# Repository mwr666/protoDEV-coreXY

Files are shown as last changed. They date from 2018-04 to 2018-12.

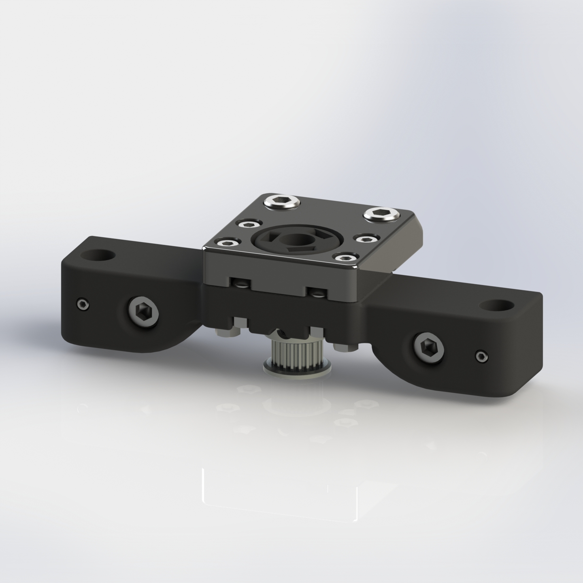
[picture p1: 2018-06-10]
render/z_axis_bottom_assembly_00.JPG

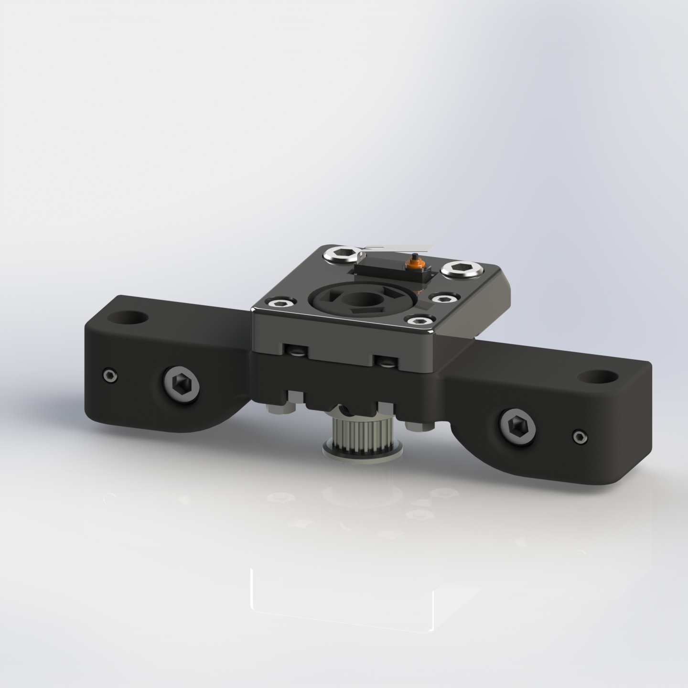
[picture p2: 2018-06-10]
render/z_axis_bottom_endstop_assembly_00.JPG

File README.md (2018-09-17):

# protoDEV coreXY
<b>coreXY direct drive extruder 3D printer running Smootieware firmware</b>

-------------------------------------------------------------------------------------------- 

<b>About:</b>
 
 What is working here? 

Hmmm... most important... it can 3d-print 24/7. 

This is not an another incomplete "work in progress" project. It's a work in progress project that has improvement in mind. 

I'm into 3d printing for few years, and active building 3d printers for most of that time. Learned a lot thanks to the community... 
and specially from community based systems like Prusa's. Internet is a place were some got news, youtube, porn... 
and some having nerd stuff... software, mechanical, electrical and electronics articles, blogs, vlogs, faqs etc. 
If you are a tech Nerd just like me, you can find tons of very interesting educational articles that can build up your knowledge until... 
for me everything ended up here on GitHub. Why? because was living the 3d printer hype and tested all the bullshit and non-bulshit projects on te planet. 

Now it's time to share some of the knowledge just like all those people all over the world shared with me. 
 
 My goal is to gather some people that will/want to build, use and improve the project.
 I've spent over 3 months working on the Cad3D part (SolidWorks) of the project to make parts simple to print and simple for makers to assembly.
 The most of those 3 months was a the path of math, symetry, mechanics... and off course... aggressive wife :P
 Then had to spent some time working on some moddifications to Smoothieware firmware and hardware just to suit the system.
 After that been studying how printer moves in slo-mo to further improve the config and mechanics.
 After builiding & testing several machine variations, got to a place where the machine just after proper setup and calibration works without ANY failure within last several months.
 
 My main goal for the system was to print with speed and quality parameters equal or beyond the market systems at under 1000 euro price tag. 
 
-------------------------------------------------------------------------------------------- 
 
<b>Features:</b>

 * build plate 245 x 245 x 300 mm ( X x Y x Z ) 
 * 32bit Smoothieware firmware for smooth motion
 * e3d volcano hotend with hartened steel 0.4mm nozzle
 * TMC2208 silent stepper drivers - spread cycle setup with step interpolarisation 1/256 
 * geared (3:1) direct drive extuder with Bondtech dual drive gears(simpler and more reliable printing then bowden)
 * max speed up to 300mm/s 
 * heated build plate with PET film surface for superb material adhesion 
 * support of multiple filament types (PLA, PET, TPU)
 * filament run-out sensor
 * coreXY with proper belt alignment for hi-torque and stiffness
 * hi-flow quality hotend (e3d hotend with volcano heat block) for high quality and fast printing
 * all axis with 2x higher mechanical resolution at same step rate (0.9deg 1/8 step = 1.8deg 1/16 step)
 * one motor doubble z-axis (no shaft sync problems)
 * all axis motors mounted at bottom of printer to lower the center of gravity  
 * all of non-printed parts was selected to be worldwide availabe and have resonable price to quality ratio.
 * enclosure
 * automatic nozzle cleaner
 * automatic parts removal ( if got time or need for this add on to work - i've designed it and printed just waiting for software )

-------------------------------------------------------------------------------------------- 
 
<b>TODO:</b>

 * add enclosure files prepared for laser cutting

 * find quiet print cooling fans replacement
 
 * enclosure over-temperature control
 
 * 3rd party controler boards support (actual controler price to high?)
 
 * apr addon (automatic parts removal) test and firmware development for batch 3d printing
 
 * <font color="green"><s>add latest 24V-hiwin-tmc2208 project files</s> <b>*done</b></font> 
 
 * cleanup in filenames / solidworks project
 
 * <font color="green"><s>cleanup in stl folder (right now it's pure project .stl dump, so lots of files not need to be printed)</s> <b>*done</b></font>
 
 * heatbed build instructions
 
 * <font color="green"><s>list of parts</s> <b>*done</b></font>
 
 * build instruction
 
 * firmware/software manual
 
 * BOM for all non-printed parts
 
*  <font color="green"><s>test 24V system theoretical print speed >375mm/s</s> <b>*done & working</b></font>
 
 * <font color="green"><s>build a test Hiwin x-axis</s> <b>*done & working</b></font>
 
*  <font color="red"><s>build a test carbon fiber rods + igus bearings x-axis</s> <b>*done - don't like it</b></font>
 
 * ???

--------------------------------------------------------------------------------------------
 
<b>Contact: mw@protodev.pl</b>

<b>https://www.thingiverse.com/thing:2119644 big thx for superb spool system from Spanner Hands http://www.spannerhands.co.uk/<b>

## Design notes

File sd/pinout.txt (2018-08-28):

P1.21		LED3		Pad4		led4		            h/w PWM capable. can be free if leds_disable is set true in config.
P1.24		-		    Pad7		alpha_min_endstop		h/w PWM capable
P3.26		-			Pad14		spare					used for encoder pin for all panels, h/w PWM capable

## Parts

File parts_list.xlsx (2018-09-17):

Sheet: part list
no. | part name | type | subtype | attribute | qty. | pcs/pack | price per pack(PLN) | qty. | total (PLN) | shop link
1 | alu square pipe | shop part | 20x20mm | 373mm | 1 |  |  |  | 0
2 | alu-profil | openbeam | 1515 | 240mm | 1 |  |  |  | 0
3 | alu-profil | T-Slot | 2020 | 360mm | 15 |  |  |  | 0
4 | alu-profil | T-Slot | 2020 | 600mm | 4 |  |  |  | 0
5 | alu-profil | T-Slot | 2020 | 95mm | 1 |  |  |  | 0
6 | corner | T-Slot | 2020 |  | 34 |  |  |  | 0
7 | 3-way connector | T-Slot | 2020 |  | 8 |  |  |  | 0
8 | half-nut | T-Slot | M3 |  | 52 |  |  |  | 0
9 | nut | T-Slot | M3 |  | 10 |  |  |  | 0
10 | nut | T-Slot | M5 |  | 108 |  |  |  | 0
11 | lead screw | shop part | TR8x8 | 400mm | 2 | 1 | 40 | 2 | 80 | https://blackfrog.pl/sruba-trapezowa-t8-z-nakretka-fi-8mm-skok-1mm-dl-400-mm-p-710.html
12 | leveling nut | shop part | M3 |  | 3 |  |  |  | 0
13 | bed spring | shop part |  |  | 3 |  |  |  | 0
14 | anti-backlash nut | shop part | TR8x8 |  | 2 | 1 | 25 | 2 | 50 | https://blackfrog.pl/nakretka-bezluzowa-sruba-t8-skok-8-mm-p-1149.html
15 | laminator roller | shop part |  |  | 2 |  |  |  | 0
16 | glass | shop part | borosilicate | 280x280mm | 1 | 1 | 195 | 1 | 195 | local glass shop
17 | thermal cover | shop part | cork | 280x280mm | 1 |  |  |  | 0
18 | heater | shop part | silicone | 280x280mm | 1 |  |  |  | 0
19 | e3d volcano block | shop part |  |  | 1 | 1 | 95 | 1 | 95 | https://blackfrog.pl/blok-grzejny-e3d-volcano-p-988.html
20 | e3d v6 direct full kit | shop part |  |  |  | 1 | 280 | 1 | 280 | https://blackfrog.pl/glowica-e3d-v6-175-12v-direct-full-kit-p-245.html
21 | volcano 0.4mm hartened steel nozzle | shop part |  |  |  | 1 | 95 | 1 | 95 | https://blackfrog.pl/dysza-volcano-e3d-stal-utwardzana-175-04-p-982.html
22 | e3d heater cartige 104GT-2 | shop part |  |  |  | 1 | 31 | 1 | 31 | https://blackfrog.pl/termistor-semitec-104gt-2-w-obudowie-p-783.html
23 | heater cartige | shop part | 12V | 40W | 1 |  |  |  | 0
24 | thermistor | shop part | Semitec |  | 2 |  |  |  | 0
25 | e3d Semitec thermistor cartige | shop part |  |  | 1 |  |  |  | 0
26 | door_hinge_shaft (alu-rod) | shop part | 5mm | 37mm | 2 |  |  |  | 0
27 | alu rod | shop part | 5mm | 32mm | 1 |  |  |  | 0
28 | alu rod | shop part | 5mm | 490mm | 2 |  |  |  | 0
29 | steel rod | shop part | 3mm | 30mm | 2 |  |  |  | 0
30 | steel rod | shop part | 8mm | 390mm | 4 |  |  |  | 0
31 | steel rod | shop part | 8mm | 217mm | 2 |  |  |  | 0
32 | fitting | shop part | PTFE | PC6-M6 | 2 |  |  |  | 0
33 | microswitch endstop | shop part |  |  | 4 |  |  |  | 0
34 | microswitch endstop with roller | shop part |  |  | 1 |  |  |  | 0
35 | NEMA17 200 step stepper motor | shop part | 17HS1070-C5X | 34mm | 1 |  |  |  | 0
36 | NEMA17 400 step stepper motor | shop part | 42BYGHM809 | 48mm | 3 |  |  |  | 0
37 | heatsink | shop part |  | 40x40x11mm | 3 |  |  |  | 0
38 | geared motor | shop part | XH-25D | 6VDC 275RPM | 1 |  |  |  | 0
39 | extruder gear | shop part | MK7 |  | 1 | 1 | 7.99 | 1 | 7.99 | http://electropark.pl/radelka/4433-kolo-zebate-ekstrudera-mk7-radelko.html
40 | fan | shop part | 3010 | 12V | 3 |  |  |  | 0
41 | extruder spring | shop part |  |  | 2 |  |  |  | 0
42 | diode smoother board | shop part | MKS |  | 4 | 1 | 16 | 4 | 64 | https://blackfrog.pl/mks-smoother-filtr-diodowy-p-1057.html
43 | lcd control panel | shop part | Sumbeam 2.0 |  | 1 |  |  |  | 0
44 | 3rd party smoothieboard rev.C | shop part | Sumbeam 2.0 |  | 1 |  |  |  | 0
45 | neo_magnet_4mm_x_4mm | shop part |  |  | 6 |  |  |  | 0
46 | dial_sticker_feet | shop part |  |  | 4 |  |  |  | 0
47 | tower pro sg90 hobby servo (full kit) | shop part |  |  | 1 |  |  |  | 0
48 | nozzle cleaner rubber | shop part |  |  | 1 |  |  |  | 0
49 | expansion board | private part | Sumbeam 2.0 |  | 1 |  |  |  | 0
50 | memory card | shop part | microSD | <4GB | 1 |  |  |  | 0
51 | memory card | shop part | SDcard | <32GB | 1 |  |  |  | 0
52 | stepper driver with heatsink | shop part | TMC2208 |  | 4 | 1 | 46 | 4 | 184 | https://blackfrog.pl/silentstepstick-tmc2208-watterott-p-1271.html
53 | power socket | shop part | 3 Pin IEC320 C14 | 10A 250V | 1 |  |  |  | 0
54 | psu | shop part | Meanwell | 12V 300W | 1 | 1 | 120 | 1 | 120 | http://allegro.pl/zasilacz-led-modulowy-montazowy-12v-300w-25a-i7308720266.html
55 | psu | shop part | Bergmen | 24V 150W | 1 | 1 | 240.9 | 1 | 240.9 | https://sklep.bergmen.pl/storm-150w-24vdc-6-25a-ip68,3,2472,1605
56 | linear bearing | bearing | LM8UU |  | 4 | 1 | 2.75 | 4 | 11 | http://allegro.pl/lozyska-liniowe-fi8-8mm-lm8uu-reprap-drukarka-3d-i6099245510.html
57 | ball bearing | bearing | 608ZZ |  | 4 | 1 | 1 | 4 | 4 | http://allegro.pl/608-zz-lozysko-kulkowe-8x22x7-mm-cnc-fv-23-i6754089162.html
58 | ball bearing | bearing | F623ZZ |  | 4 | 1 | 2.8 | 4 | 11.2 | http://allegro.pl/f623-zz-lozysko-z-kolnierzem-flansza-3x10x4-reprap-i6487218476.html
59 | ball bearing | bearing | 625zz |  | 10 | 1 | 1 | 10 | 10 | http://allegro.pl/625-zz-lozysko-kulkowe-5x16x5-mm-cnc-fv-23-i6487158324.html
60 | ball bearing | bearing | 623zz |  | 17 | 1 | 1 | 17 | 17 | http://allegro.pl/623-zz-lozysko-kulkowe-3x10x4-mm-cnc-fv-23-i6487155806.html
61 | build plate belt | belt | PET | 242mm | 1 |  |  |  | 0
62 | belt | GT2 | closed-loop | 120-130mm | 2 | 1 | 10 | 2 | 20 | http://allegro.pl/pasek-zebaty-petla-130-mm-gt2-szer-6mm-reprap-cnc-i7169467426.html
63 | belt | GT2 | closed-loop | 720mm | 1 | 1 | 22 | 1 | 22 | http://allegro.pl/pasek-zebaty-petla-752-mm-gt2-szer-6mm-reprap-cnc-i7169534315.html
64 | belt | GT2 | open-loop | <1422 | 2 | 1000 | 6.9 | 2 | 13.8 | http://allegro.pl/pasek-zebaty-gt2-6mm-100cm-reprap-drukarka-3d-i7270779540.html
65 | pully | GT2 | 20T | 8mm | 2 | 1 | 13 | 2 | 26 | https://blackfrog.pl/zebatka-gt2-20-zebow-otwor-fi-8-pasek-6-mm-p-158.html
66 | pully | GT2 | 20T | 5mm | 7 | 1 | 8.49 | 7 | 59.43 | http://allegro.pl/zebatka-reprap-gt2-20-zebow-5mm-3d-cnc-i6099125153.html
67 | rail | MGH | 12H | 360mm | 3 | 100 | 70 | 4 | 280 | https://blackfrog.pl/szyna-liniowa-mgnr-12-dlugosc-10-cm-p-768.html
68 | carriage | MGH | 12H |  | 3 | 1 | 165 | 2 | 330 | https://blackfrog.pl/wozek-hiwin-mgn12h-p-765.html
69 | hex nut | nut | M3 |  | 74 | 10 | 1.5 | 8 | 12 | http://allegro.pl/nakretki-nakretka-m3-czarna-10szt-komplet-oksyda-i5080287746.html
70 | prevailing torque hex nut | nut | M8 |  | 1 | 10 | 4.8 | 1 | 4.8 | http://allegro.pl/nakretka-samohamowna-czarna-oksyda-m8-10szt-i6842846781.html
71 | socket head cap screw | screw | M8 | 80mm | 1 | 5 | 5 | 1 | 5 | http://allegro.pl/sruba-imbusowa-czarna-m8x80-gniazdo-imbus-5szt-i6596358554.html
72 | socket head cap screw | screw | M5 | 25mm | 4 | 10 | 3.2 | 1 | 3.2 | http://allegro.pl/sruba-imbusowa-czarna-m5x25-gniazdo-imbus-10szt-i5045808605.html
73 | socket head cap screw | screw | M5 | 20mm | 16 | 10 | 2.9 | 2 | 5.8 | http://allegro.pl/sruba-imbusowa-czarna-m5x20-gniazdo-imbus-10szt-i7140410516.html
74 | hex cap screw | screw | M5 | 16mm | 1 | 1 | 1 | 1 | 1
75 | socket head cap screw | screw | M5 | 10mm | 5 | 10 | 2.5 | 1 | 2.5 | http://allegro.pl/sruba-imbusowa-czarna-m5x10-gniazdo-imbus-10szt-i5044828525.html
76 | socket head cap screw | screw | M5 | 8mm | 76 | 10 | 2.6 | 8 | 20.8 | http://allegro.pl/sruba-imbusowa-czarna-m5x8-gniazdo-imbus-10szt-i5045808558.html
77 | socket head cap screw | screw | M5 | 6mm | 14 | 10 | 2.8 | 2 | 5.6 | http://allegro.pl/sruba-imbusowa-czarna-m5x6-gniazdo-imbus-10szt-i5045808600.html
78 | socket set screw flat point | screw | M4 | 6mm | 32 |  |  |  | 0
79 | socket head cap screw | screw | M3 | 45mm | 23 | 5 | 2.9 | 5 | 14.5 | http://allegro.pl/sruba-imbusowa-czarna-m3x45-gniazdo-imbus-5szt-i5039141859.html
80 | socket head cap screw | screw | M3 | 40mm | 12 | 5 | 2.4 | 3 | 7.2 | http://allegro.pl/sruba-imbusowa-czarna-m3x40-gniazdo-imbus-5szt-i5063374831.html
81 | socket head cap screw | screw | M3 | 35mm | 14 | 10 | 3.3 | 2 | 6.6 | http://allegro.pl/sruba-imbusowa-czarna-m3x35-gniazdo-imbus-10szt-i5176356584.html
82 | socket head cap screw | screw | M3 | 25mm | 12 | 10 | 2.8 | 2 | 5.6 | http://allegro.pl/sruba-imbusowa-czarna-m3x25-gniazdo-imbus-10szt-i5415086316.html
83 | socket button head cap screw | screw | M3 | 25mm | 8 | 10 | 1.6 | 1 | 1.6 | http://allegro.pl/sruba-kulista-czarna-m3x25-gniazdo-imbus-10szt-i5214620250.html
84 | socket button head cap screw | screw | M3 | 20mm | 22 | 10 | 1.5 | 3 | 4.5 | http://allegro.pl/sruba-kulista-czarna-m3x20-gniazdo-imbus-10szt-i5214620056.html
85 | socket head cap screw | screw | M3 | 20mm | 37 | 10 | 2.5 | 4 | 10 | http://allegro.pl/sruba-imbusowa-czarna-m3x20-gniazdo-imbus-10szt-i5057841873.html
86 | socket head cap screw | screw | M3 | 16mm | 10 | 10 | 2.2 | 1 | 2.2 | http://allegro.pl/sruba-imbusowa-czarna-m3x16-gniazdo-imbus-10szt-i5184033908.html
87 | socket button head cap screw | screw | M3 | 16mm | 16 | 10 | 1.3 | 2 | 2.6 | http://allegro.pl/sruba-kulista-czarna-m3x16-gniazdo-imbus-10szt-i5214620038.html
88 | socket button head cap screw | screw | M3 | 12mm | 6 | 10 | 1.1 | 1 | 1.1 | http://allegro.pl/sruba-kulista-czarna-m3x12-gniazdo-imbus-10szt-i5142905904.html
89 | socket head cap screw | screw | M3 | 10mm | 10 | 10 | 1.7 | 1 | 1.7 | http://allegro.pl/sruba-imbusowa-czarna-m3x10-gniazdo-imbus-10szt-i5006971342.html
90 | socket button head cap screw | screw | M3 | 10mm | 34 | 10 | 1.1 | 4 | 4.4 | http://allegro.pl/sruba-kulista-czarna-m3x10-gniazdo-imbus-10szt-i5089594834.html
91 | socket button head cap screw | screw | M3 | 8mm | 29 | 10 | 1.5 | 3 | 4.5 | http://allegro.pl/sruba-kulista-czarna-m3x8-gniazdo-imbus-10szt-i5315915867.html
92 | socket head cap screw | screw | M3 | 8mm | 69 | 10 | 1.9 | 7 | 13.3 | http://allegro.pl/sruba-imbusowa-czarna-m3x8-gniazdo-imbus-10szt-i5113065217.html
93 | socket set screw flat point | screw | M3 | 6mm | 39 | 10 | 1.4 | 4 | 5.6 | http://allegro.pl/sruba-dociskowa-czarna-m3x6-gniazdo-imbus-10szt-i5088078246.html
94 | socket head cap screw | screw | M3 | 6mm | 6 | 10 | 1.9 | 1 | 1.9 | http://allegro.pl/sruba-imbusowa-czarna-m3x6-gniazdo-imbus-10szt-i5717390190.html
95 | socket button head cap screw | screw | M3 | 6mm | 27 | 10 | 1 | 3 | 3 | http://allegro.pl/sruba-kulista-czarna-m3x6-gniazdo-imbus-10szt-i6789930676.html
96 | socket head cap screw | screw | M2.5 | 12mm | 5 | 10 | 2.3 | 1 | 2.3 | http://allegro.pl/sruba-imbusowa-czarna-m2-5x12-gniazdo-imbus-10szt-i5214620364.html
97 | flat washer | washer | M3 |  | 8 | 20 | 1.2 | 1 | 1.2 | http://allegro.pl/podkladka-czarna-m3-komplet-20szt-oksyda-i5080289361.html
98 | spring washer (from NEMA 17 stepper motor) | shop part |  |  | 1 |  |  |  | 0
99 | bed_clamp_bottom.STL | printed part |  |  | 3 |  |  |  | 0
100 | bed_clamp_top.STL | printed part |  |  | 3 |  |  |  | 0
101 | top_base.STL | printed part |  |  | 2 |  |  |  | 0
102 | lift_right_side_base.STL | printed part |  |  | 1 |  |  |  | 0
103 | z_axis_endstop_bumper.STL | printed part |  |  | 1 |  |  |  | 0
104 | bed_clamp_mount_side.STL | printed part |  |  | 1 |  |  |  | 0
105 | bed_clamp_mount_side_cover.STL | printed part |  |  | 1 |  |  |  | 0
106 | bed_clamp_mount_side2_cover.STL | printed part |  |  | 1 |  |  |  | 0
107 | bed_clamp_mount_side2.STL | printed part |  |  | 1 |  |  |  | 0
108 | lift_left_side_base.STL | printed part |  |  | 1 |  |  |  | 0
109 | back_left_roller_motor_mount.STL | printed part |  |  | 1 |  |  |  | 0
110 | back_right_roller_mount.STL | printed part |  |  | 1 |  |  |  | 0
111 | front_right_roller_mount.STL | printed part |  |  | 1 |  |  |  | 0
112 | front_left_roller_mount.STL | printed part |  |  | 1 |  |  |  | 0
113 | apr_shaft_beam.STL | printed part |  |  | 2 |  |  |  | 0
114 | apr_gears.STL | printed part |  |  | 1 |  |  |  | 0
115 | bottom_base.STL | printed part |  |  | 1 |  |  |  | 0
116 | blocker_cover.STL | printed part |  |  | 1 |  |  |  | 0
117 | blocker_lead_screw_8mm.STL | printed part |  |  | 1 |  |  |  | 0
118 | bottom_base_endstop.STL | printed part |  |  | 1 |  |  |  | 0
119 | blocker_cover_endstop.STL | printed part |  |  | 1 |  |  |  | 0
120 | blocker_lead_screw_8mm.STL | printed part |  |  | 1 |  |  |  | 0
121 | motor_holder_cover.STL | printed part |  |  | 2 |  |  |  | 0
122 | motor_holder.STL | printed part |  |  | 2 |  |  |  | 0
123 | z_motor_holder_top_v2.STL | printed part |  |  | 1 |  |  |  | 0
124 | z_motor_holder_v2.STL | printed part |  |  | 1 |  |  |  | 0
125 | z_motor_holder_cover_v2.STL | printed part |  |  | 1 |  |  |  | 0
126 | z_motor_holder_top_cover_v2.STL | printed part |  |  | 1 |  |  |  | 0
127 | z_axis_square_pipe_mount.STL | printed part |  |  | 2 |  |  |  | 0
128 | motor_block_bearing.STL | printed part |  |  | 4 |  |  |  | 0
129 | motor_block_bearing_cover.STL | printed part |  |  | 2 |  |  |  | 0
130 | printable_20T_GT2_idler_tooth.STL | printed part |  |  | 6 |  |  |  | 0
131 | printable_20T_GT2_idler_smooth.STL | printed part |  |  | 2 |  |  |  | 0
132 | idler_holder_doubble_left_v3.STL | printed part |  |  | 1 |  |  |  | 0
133 | idler_holder_doubble_right_v3.STL | printed part |  |  | 1 |  |  |  | 0
134 | rail_holder_left_front.STL | printed part |  |  | 1 |  |  |  | 0
135 | rail_holder_left_back.STL | printed part |  |  | 1 |  |  |  | 0
136 | rail_holder_endstop.STL | printed part |  |  | 1 |  |  |  | 0
137 | rail_holder_right_back.STL | printed part |  |  | 1 |  |  |  | 0
138 | y_carrige_cover_left.STL | printed part |  |  | 1 |  |  |  | 0
139 | y_carrige_cover_right.STL | printed part |  |  | 1 |  |  |  | 0
140 | y_carriage_left.STL | printed part |  |  | 1 |  |  |  | 0
141 | y_carriage_right.STL | printed part |  |  | 1 |  |  |  | 0
142 | hiwin_block.STL | printed part |  |  | 1 |  |  |  | 0
143 | carriage_cable_holder.STL | printed part |  |  | 1 |  |  |  | 0
144 | 33tooth_spur_gear.STL | printed part |  |  | 1 |  |  |  | 0
145 | fan_mount_v12.STL | printed part |  |  | 1 |  |  |  | 0
146 | fan_cover_front.STL | printed part |  |  | 1 |  |  |  | 0
147 | fan_cover.STL | printed part |  |  | 1 |  |  |  | 0
148 | button.STL | printed part |  |  | 1 |  |  |  | 0
149 | gear_cover.STL | printed part |  |  | 1 |  |  |  | 0
150 | geared_extruder_3to1_hiwin.STL | printed part |  |  | 1 |  |  |  | 0
151 | ac_plug_mount_cover.STL | printed part |  |  | 1 |  |  |  | 0
152 | ac_plug_mount_base.STL | printed part |  |  | 1 |  |  |  | 0
153 | mks_4x_smoother_mount.STL | printed part |  |  | 1 |  |  |  | 0
154 | mks_4x_smoother_mount_spacer.STL | printed part |  |  | 1 |  |  |  | 0
155 | board_holder.STL | printed part |  |  | 1 |  |  |  | 0
156 | vent_board_back_v2.STL | printed part |  |  | 1 |  |  |  | 0
157 | filament_sensor_holder.STL | printed part |  |  | 1 |  |  |  | 0
158 | filament_sensor_base_spool_holder.STL | printed part |  |  | 1 |  |  |  | 0
159 | filament sensor_cover_spool_holder.STL | printed part |  |  | 1 |  |  |  | 0
160 | lid_v3_0_1kg_Spool.STL | printed part |  |  | 1 |  |  |  | 0
161 | base_v3_0_1kg_Spool.STL | printed part |  |  | 1 |  |  |  | 0
162 | 20x20_T_Slot_MOUNT_v1_0.STL | printed part |  |  | 1 |  |  |  | 0
163 | clasp_bracket_v2_0.STL | printed part |  |  | 1 |  |  |  | 0
164 | semi_flex_clasp_v2_0.STL | printed part |  |  | 1 |  |  |  | 0
165 | flex_seal_v3_0_1kg_Spool.STL | printed part |  |  | 1 |  |  |  | 0
166 | panel_cover_front.STL | printed part |  |  | 1 |  |  |  | 0
167 | panel_cover_bottom.STL | printed part |  |  | 1 |  |  |  | 0
168 | arrow_button.STL | printed part |  |  | 2 |  |  |  | 0
169 | blank_button.STL | printed part |  |  | 2 |  |  |  | 0
170 | reset_button.STL | printed part |  |  | 1 |  |  |  | 0
171 | psu_holder.STL | printed part |  |  | 1 |  |  |  | 0
172 | extruder_cable_cover.STL | printed part |  |  | 1 |  |  |  | 0
173 | magnetic_bottom.STL | printed part |  |  | 1 |  |  |  | 0
174 | magnetic_top.STL | printed part |  |  | 1 |  |  |  | 0
175 | handle_front.STL | printed part |  |  | 1 |  |  |  | 0
176 | door_hinge_1b.STL | printed part |  |  | 2 |  |  |  | 0
177 | 2020_140mm_fan_mount.STL | printed part |  |  | 1 |  |  |  | 0
178 | 2020_140mm_fan_mount_mirror.STL | printed part |  |  | 1 |  |  |  | 0
179 | 2020_top_cover_corner.STL | printed part |  |  | 4 |  |  |  | 0
180 | 2020_cover_middle_section.STL | printed part |  |  | 2 |  |  |  | 0
181 | 2020_cover_middle_Handle_section.STL | printed part |  |  | 2 |  |  |  | 0
182 | 2020_bottom_corner_cover.STL | printed part |  |  | 4 |  |  |  | 0
183 | 2020_cover_middle_section.STL | printed part |  |  | 4 |  |  |  | 0
184 | 2020_corner_cover_mount_top_spool_holder.STL | printed part |  |  | 1 |  |  |  | 0
185 | 2020_corner_cover_mount.STL | printed part |  |  | 4 |  |  |  | 0
186 | 2020_corner_cover_mount_top.STL | printed part |  |  | 4 |  |  |  | 0
187 | 2020_corner_cover_mount_top_screw_hole.STL | printed part |  |  | 3 |  |  |  | 0
188 | handle.STL | printed part |  |  | 2 |  |  |  | 0
189 | door_hinge_1a.STL | printed part |  |  | 2 |  |  |  | 0
190 | wiper_v2.STL | printed part |  |  | 1 |  |  |  | 0
191 | 2020_servo_holder.STL | printed part |  |  | 1 |  |  |  | 0
192 | cover_side_plate | laser-cut |  |  | 1 |  |  |  | 0
193 | cover_ac_power_in_side_plate | laser-cut |  |  | 1 |  |  |  | 0
194 | cover_back_plate | laser-cut |  |  | 1 |  |  |  | 0
195 | cover_front_plate | laser-cut |  |  | 1 |  |  |  | 0
196 | cover_middle_plate | laser-cut |  |  | 1 |  |  |  | 0
197 | door_plate | laser-cut |  |  | 1 |  |  |  | 0
198 | cover_top_plate | laser-cut |  |  | 1 |  |  |  | 0
199 | cover_bottom_plate | laser-cut |  |  | 1 |  |  |  | 0
 |  |  |  |  |  |  |  |  | 2401.82
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

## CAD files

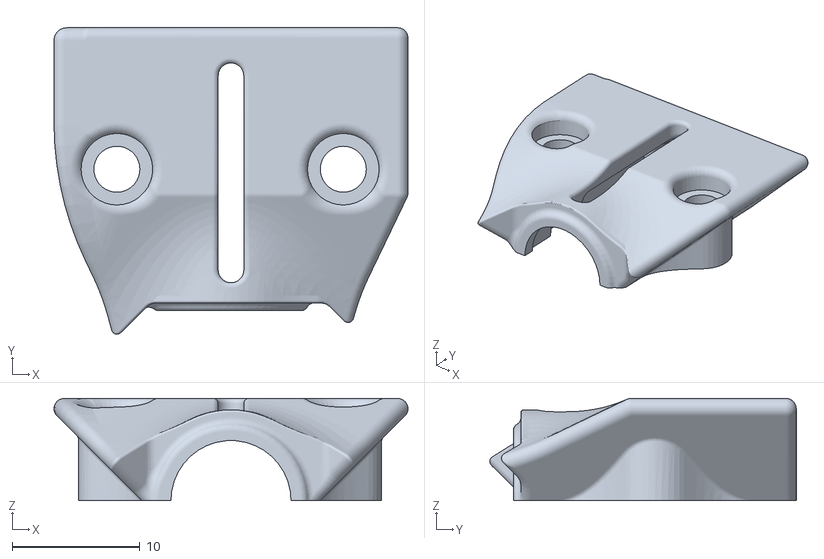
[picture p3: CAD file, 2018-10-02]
stl/x_axis_carriage_plate/parts/bondtech_gears_extruder/bondtech_main_block_cover_v3.STL
27.7 x 24.0 x 7.99

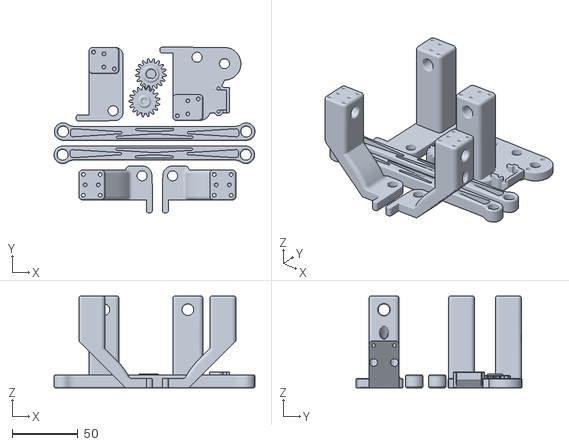
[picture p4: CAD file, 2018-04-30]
stl/apr_parts_plate/apr_parts_plate.stl
153.4 x 126.7 x 70.0

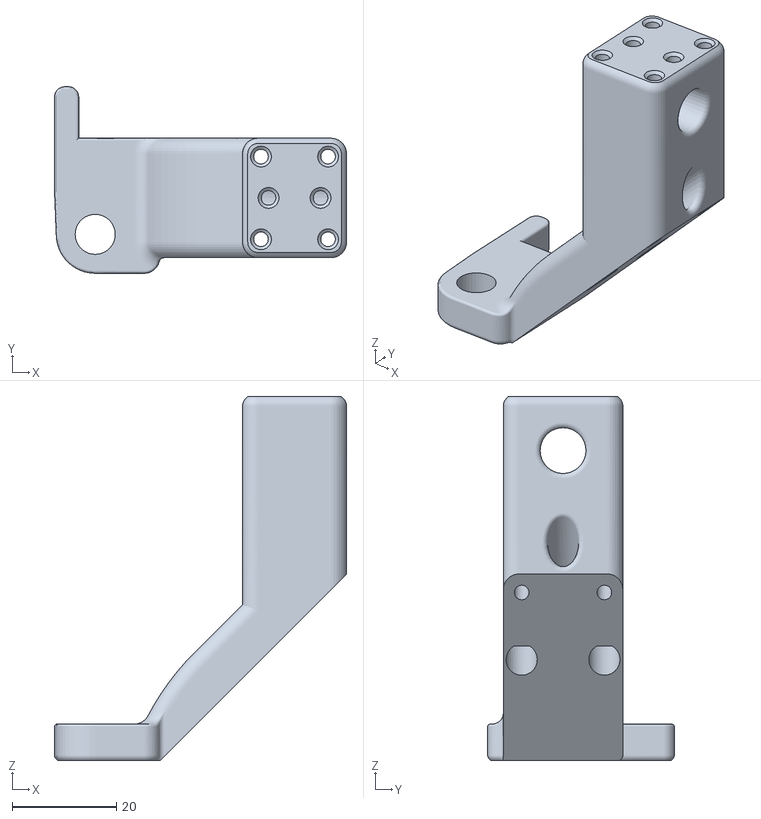
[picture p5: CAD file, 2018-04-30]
stl/apr_parts_plate/parts/back_right_roller_mount.STL
56.2 x 35.9 x 70.0

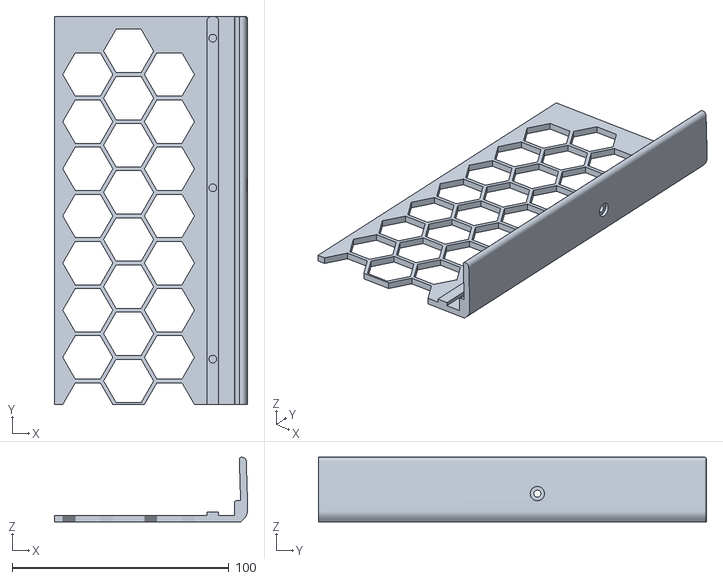
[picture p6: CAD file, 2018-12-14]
stl/inner_back_top_left.STL
89.0 x 178.9 x 29.8

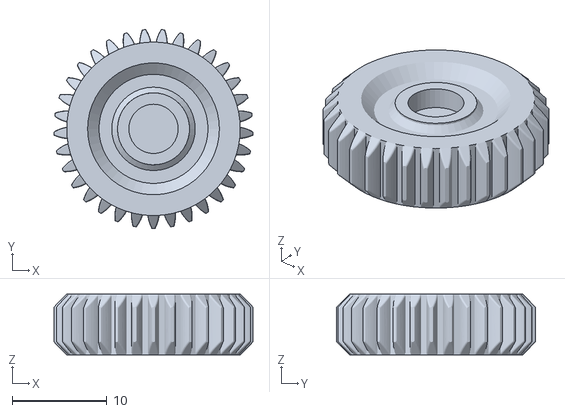
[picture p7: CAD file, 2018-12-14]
stl/x_axis_carriage_plate/parts/bondtech_gears_extruder/bondtech_gear_v2.STL
21.0 x 21.0 x 6.40

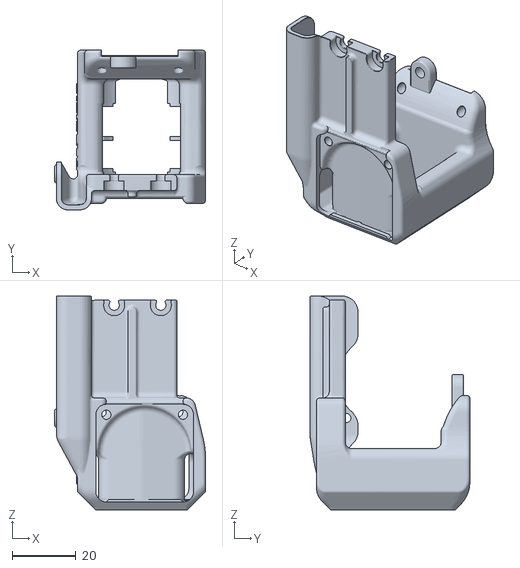
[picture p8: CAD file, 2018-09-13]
stl/x_axis_carriage_plate/parts/fan_mount_v12.STL
47.3 x 50.0 x 67.0

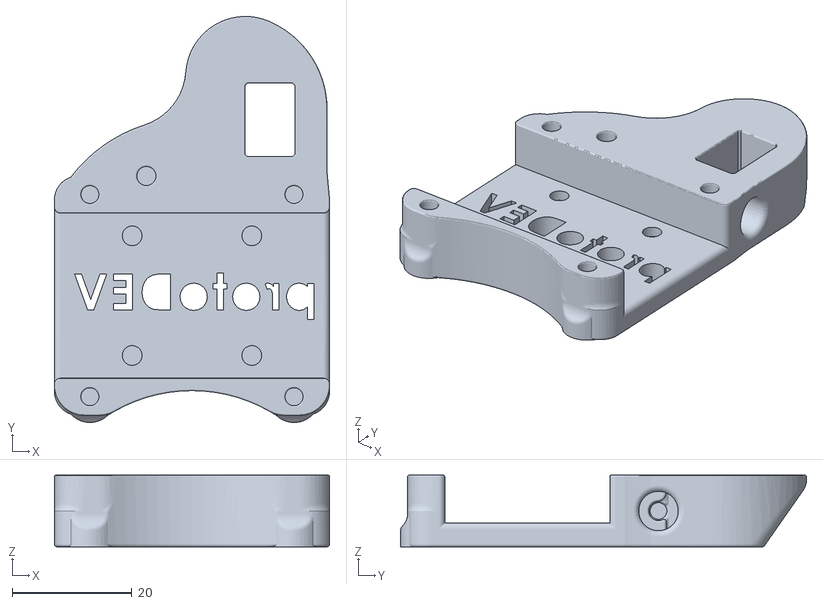
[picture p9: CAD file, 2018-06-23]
stl/y_axis_parts_plate/parts/y_carriage_cover_right.STL
46.0 x 67.9 x 12.0

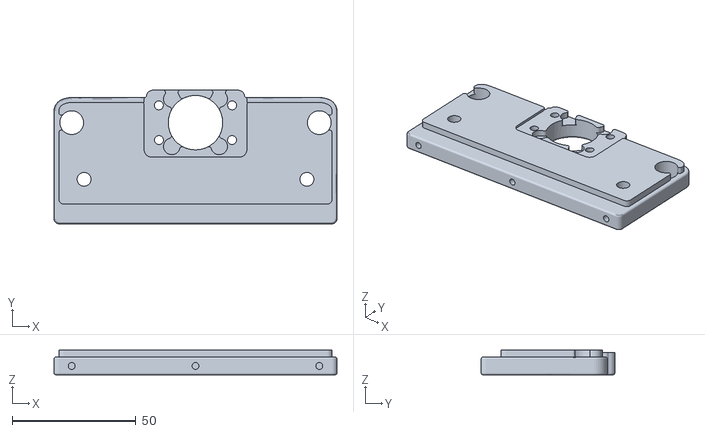
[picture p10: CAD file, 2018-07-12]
stl/z_axis_parts_plate/parts/blocker_cover.STL
114.3 x 54.0 x 10.0

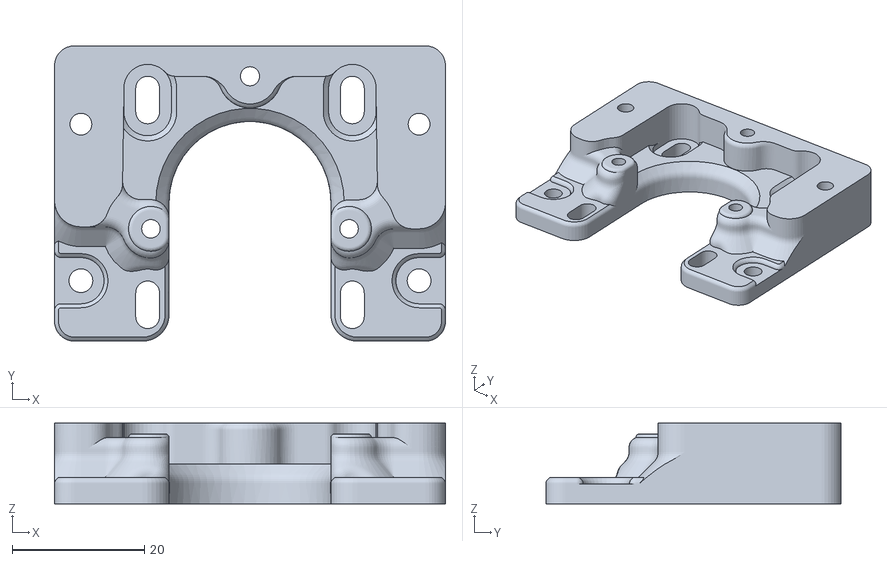
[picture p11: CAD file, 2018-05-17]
stl/z_axis_tensioner_parts_plate/parts/z_motor_holder_cover_v2.STL
59.2 x 44.7 x 12.2

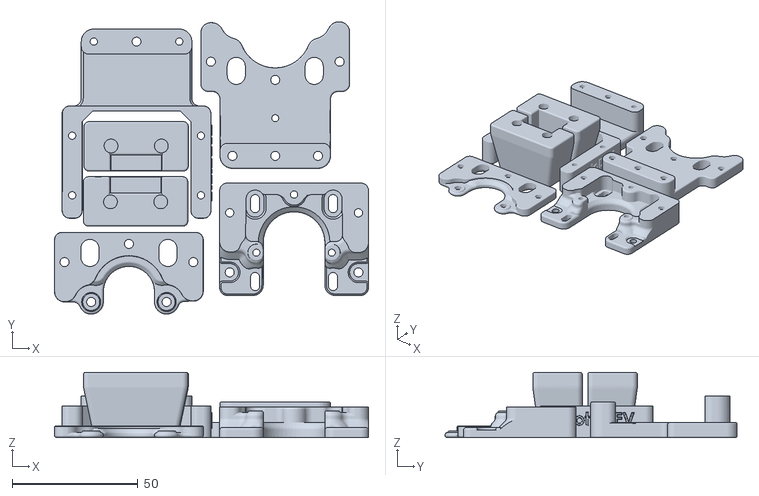
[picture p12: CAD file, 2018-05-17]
stl/z_axis_tensioner_parts_plate/z_axis_tensioner_parts_plate.stl
124.9 x 116.3 x 26.0

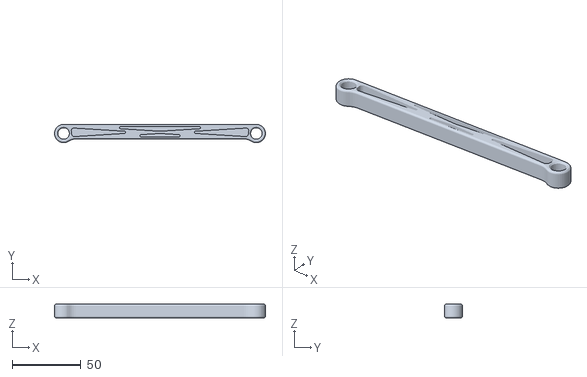
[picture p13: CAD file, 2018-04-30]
stl/apr_parts_plate/parts/apr_shaft_beam.STL
153.1 x 13.3 x 10.0

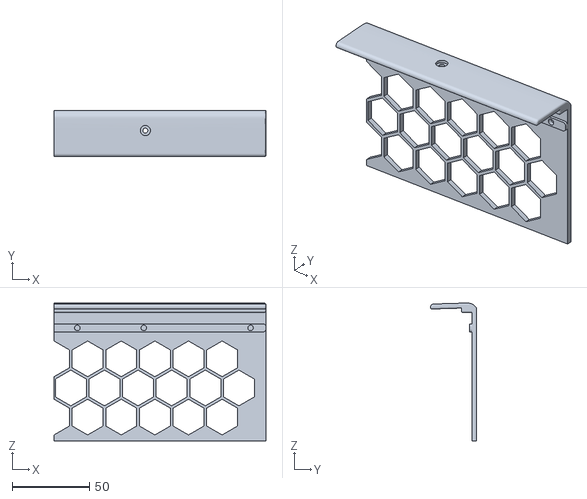
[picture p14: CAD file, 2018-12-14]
stl/inner_back_top_right.STL
137.1 x 29.8 x 89.0

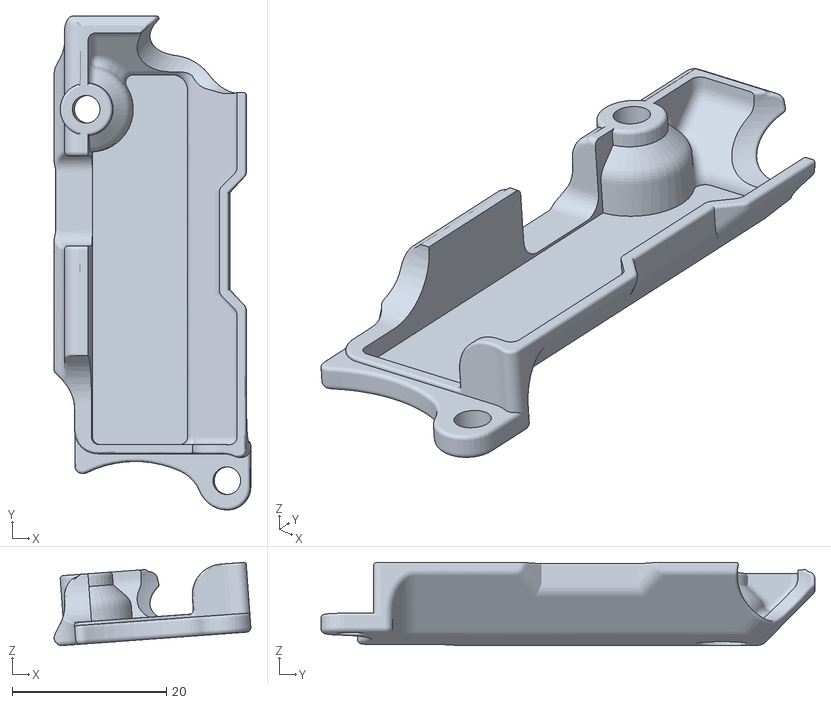
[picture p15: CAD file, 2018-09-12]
stl/x_axis_carriage_plate/parts/extruder_cable_cover.STL
25.5 x 64.1 x 10.8

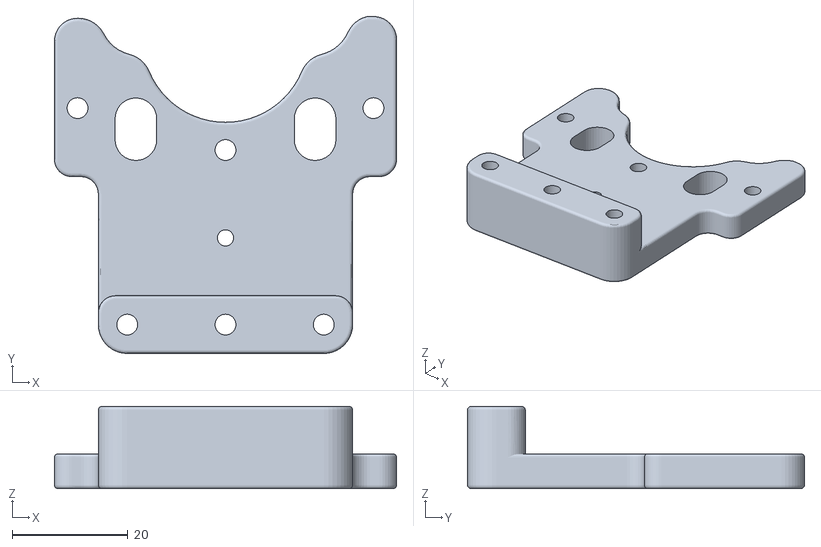
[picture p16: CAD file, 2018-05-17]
stl/z_axis_tensioner_parts_plate/parts/z_motor_holder_top_v2.STL
59.2 x 58.3 x 14.2

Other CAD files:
stl/y_axis_parts_plate/parts/y_carriage_cover_left.STL
stl/z_axis_parts_plate/parts/blocker_cover_endstop_v2.STL
stl/apr_parts_plate/parts/front_right_roller_mount.STL
stl/board_cover_back_frame.STL
stl/1cm_test_cube.stl
stl/2020_140mm_fan_mount.STL
stl/2020_140mm_fan_mount_mirror.STL
stl/2020_bottom_corner_cover.STL
stl/2020_bottom_cover_glides_mount.STL
stl/2020_corner_cover_mount.STL
stl/2020_corner_cover_mount_top.STL
stl/2020_corner_cover_mount_top_screw_hole.STL
stl/2020_corner_cover_mount_top_spool_holder.STL
stl/2020_cover_middle_Handle_section.STL
stl/2020_cover_middle_section.STL
stl/2020_servo_holder.STL
stl/2020_top_cover_corner.STL
stl/20x20_T_Slot_MOUNT_v1_0.STL
stl/Core_v3_1kg_Spool_49mm.STL
stl/ac_plug_mount_base.STL
stl/ac_plug_mount_cover.STL
stl/acin_cover.STL
stl/apr_parts_plate/parts/apr_gears.STL
stl/apr_parts_plate/parts/back_left_roller_motor_mount.STL
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

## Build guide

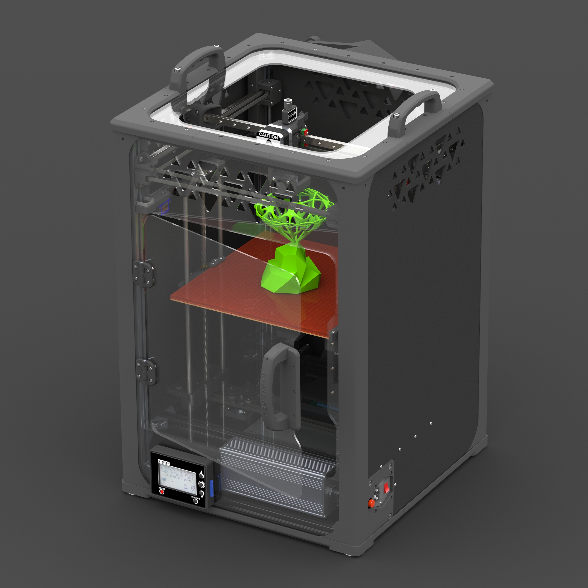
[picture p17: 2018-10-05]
render/enclosed_full_assembly_00.JPG

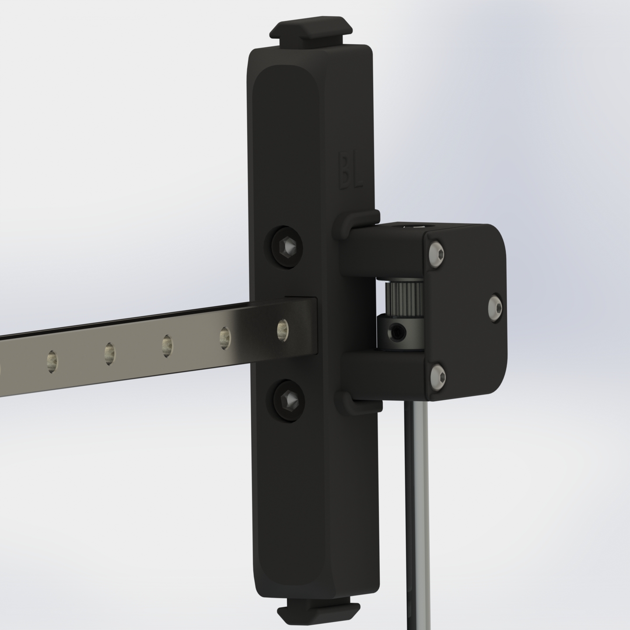
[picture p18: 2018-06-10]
render/y_axis_rail_left_assembly_03.JPG

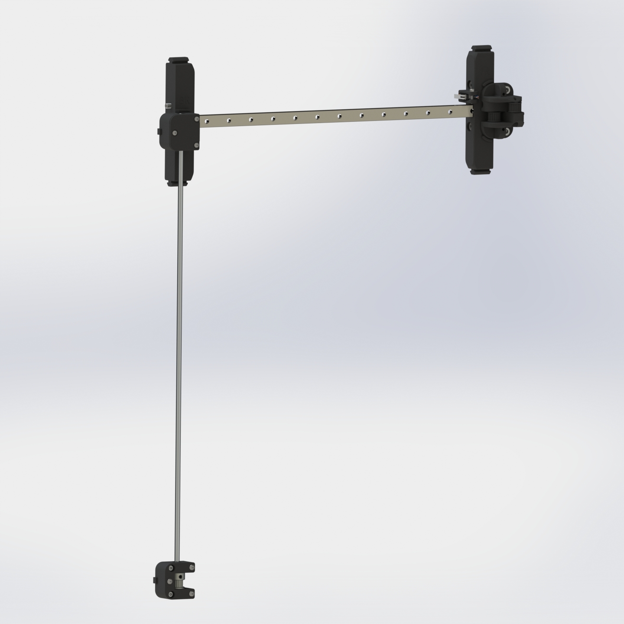
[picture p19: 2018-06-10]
render/y_axis_rail_right_assembly_00.JPG

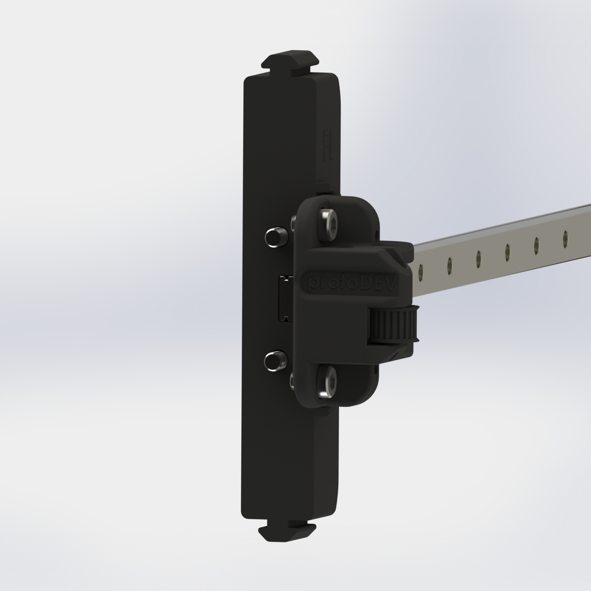
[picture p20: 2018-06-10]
render/y_axis_rail_left_assembly_04.JPG

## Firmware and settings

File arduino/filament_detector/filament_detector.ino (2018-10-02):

// nodeM esp8266 serial Filament controller 
// - use 2 inputs (microswitch, opto, hall-e etc.) to detect filament 
//   absence and control the 3dprinter suspend state by serial comand
// - semi-automatic filament changing
//      *slide filament into spool sensor for automatic nozzle heatup (slide out to cooldown)
//      *when heated up slide the filament into extruder sensor so it can be auto-loaded 
// 
// by protoDEV

// Include the Bounce2 library found here :
// https://github.com/thomasfredericks/Bounce2
#include <Bounce2.h>

#define SPOOL_PIN D6
#define EXTRUDER_PIN D5
#define LED_PIN D0

bool spoolState ;
bool extruderState ;
byte state ;
bool preheatState = false;
bool msgCode = false ;
bool msgCode2 = false ;

unsigned long previousMillis = 0;
unsigned long previousMillis2 = 0;

// constants won't change:
const long interval  = 3000;

Bounce spoolSensor = Bounce(); // Instantiate a Bounce object
Bounce extruderSensor = Bounce(); // Instantiate a Bounce object

void setup() {

  Serial.begin(115200);

  spoolSensor.attach(SPOOL_PIN, INPUT_PULLUP); // Attach the debouncer to a pin with INPUT_PULLUP mode
  spoolSensor.interval(300); // Use a debounce interval of 300 milliseconds

  extruderSensor.attach(EXTRUDER_PIN, INPUT_PULLUP); // Attach the debouncer to a pin with INPUT_PULLUP mode
  extruderSensor.interval(2000); // Use a debounce interval of 3 seconds

  spoolState = digitalRead(SPOOL_PIN);     // read the input pin
  extruderState = digitalRead(EXTRUDER_PIN);     // read the input pin
  pinMode(LED_PIN, OUTPUT); // Setup the LED
  state = stateIndicator();
}
byte stateIndicator() {

  byte state;
  bool led = false;

  if ( (spoolState == HIGH) && (extruderState == HIGH) )
  {
    led = true;
    state = 3 ; // filament fully loaded
  }
  if ( (spoolState == LOW) && (extruderState == HIGH) )
  {
    state = 2 ; // filament loaded only in extruder sensor
  }
  if ( (spoolState == HIGH) && (extruderState == LOW) )
  {
    state = 1 ; // filament loaded only in spool sensor
  }
  if ( (spoolState == LOW) && (extruderState == LOW) )
  {
    state = 0 ; // filament not loaded
  }

  digitalWrite(LED_PIN, led); // Apply new LED state

  return state ;
}

void spoolLoop()  {

  if ( spoolSensor.rose() ) {  // Call code if button transitions from LOW to HIGH
    Serial.println("\nM117");
    if ( (state == 0) && (preheatState == LOW) )  {
      preheatState = HIGH; //Toggle Preheat state ON
      Serial.println("\nM104 S220");
    }
    spoolState = HIGH; // Toggle LED ON state
  }

  if ( spoolSensor.fell() ) {  // Call code if button transitions from HIGH to LOW
    //    Serial.println();
    if (preheatState == HIGH) {
      preheatState = LOW;
      Serial.println("\nM104 S0\nM117");
    }
    if (state == 3) {
      Serial.println();
      Serial.println("suspend");
    }
    spoolState = LOW; // Toggle LED OFF state
  }

}

void extruderLoop()  {

  if ( extruderSensor.rose() ) {  // Call code if button transitions from LOW to HIGH
    if ((state == 1) && (preheatState == HIGH)) {
      preheatState = LOW ;
      Serial.println("\nM117\nM120\nG91\nG1 E80 F300\nM121\nM400\nM104 S0");
    }
    extruderState = HIGH; // Toggle state
  }

  if ( extruderSensor.fell() ) {  // Call code if button transitions from HIGH to LOW
    extruderState = LOW; // Toggle state
  }

}

void messageLoop()  {

  unsigned long currentMillis = millis();

  if ( (state == 0) || (state == 2) ) {
    if (currentMillis - previousMillis >= interval) {
      // save the last time you send M117 message
      previousMillis = currentMillis;
      if (msgCode == false) {
        Serial.println("\nM117 PLEASE CHANGE SPOOL");
        msgCode = true ;
      } else {
        Serial.println("\nM117 OUT OF FILAMENT");
        msgCode = false ;
      }
    }
  }

  if ((state == 1) && (preheatState == HIGH)) {
    if (currentMillis - previousMillis2 >= interval) {
      // save the last time you send M117 message
      previousMillis2 = currentMillis;
      if (msgCode2 == false) {
        Serial.println("\nM117 WAIT FOR HEAT UP");
        msgCode2 = true ;
      } else {
        Serial.println("\nM117 THEN INSERT FILAMENT");
        msgCode2 = false ;
      }
    }
  }

}

void loop() {

  spoolSensor.update(); // Update the Bounce instance
  extruderSensor.update(); // Update the Bounce instance
  state = stateIndicator();
  spoolLoop();
  extruderLoop();
  messageLoop();

}

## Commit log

2018-02-21 Initial upload
    Initial upload of protoDEV coreXY 3dprinter project
    [00_protoDEV_full_assembly - SPANNERHANDS_Spool_System_Wall_Mounted_Spool_Holder_Dust_Cover-1 2020_mount-1.STL, 00_protoDEV_full_assembly - SPANNERHANDS_Spool_S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]
2018-04-26 BIG UPDATE
    -list of parts
    -all needed .stl exported and proper alligned
    -new project render files
    [00_protoDEV_full_assembly - SPANNERHANDS_Spool_System_Wall_Mounted_Spool_Holder_Dust_Cover-1 2020_mount-1.STL, 00_protoDEV_full_assembly - SPANNERHANDS_Spool_S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]
2018-04-26 burp fix
    [parts_list.xlsx]
2018-04-30 apr update
    automatic part removal system stl files & updated part list
    [apr_gears.STL, apr_parts_plate.stl, apr_shaft_beam.STL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]
2018-05-16 z_axis update
    - new z axis tenssioner - smaller, simplier, cheaper
    -render added
    -new .stl files added
    - old .stl files removed
    [parts_list.xlsx, z_idler.STL, z_motor_holder.STL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]
2018-05-17 update
    new parts plate z_axis_tensioner_parts_plate.STL added
    [parts_list.xlsx, z_axis_square_pipe_mount.STL, z_axis_tensioner_parts_plate.stl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]
2018-05-17 tensioner update
    minor design update
    [z_axis_tensioner_parts_plate.stl, z_motor_holder_cover_v2.STL, z_motor_holder_top_cover_v2.STL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]
2018-05-18 update
    part list completed... so right now i can make the BOM
    [parts_list.xlsx]
2018-05-28 design update
    - x axis carriage re-design
    - part_list.xls update
    - latest renders
    - latest slic3rPE config bundle
    [30x30_fan_duct.STL, 33tooth_spur_gear.STL, button.STL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]
2018-06-10 minor_update
    -specified stepper motors in part_list.xls
    -added datasheets for some shop hardware
    -added stepper max speed calculator.xls from duet3d.dozuki.com
    [parts_list.xlsx, stepper_motor_speed.xlsx]
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2018-06-19 fan duct update
    Updated the cooling fan duct design for better air flow.
    Now the nozzle isn't cooled that much when the air flows (the previous design sometime was causing fillament jams because the nozzle was cooled by the flowing air)
    [fan_mount_v11.STL, parts_list.xlsx]
2018-06-23 latest update
    -added y_axis_parts_plate.stl
    -added .stl files for magnetic connector addon for spool system
    -updated y_carriage_covers design files
    -pudated parts_list.xlsx
    [idler_holder_doubble_left_v3.STL, idler_holder_doubble_right_v3.STL, magnetic_bottom.STL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]
2018-07-11 enclosure preview
    - enclosure preview render
    - updated ac_plug_mount_cover.STL
    for enclosure
    - updated part list.xlsx
    -added Core_v3_1kg_Spool_49mm.STL
    [Core_v3_1kg_Spool_49mm.STL, ac_plug_mount_cover.STL, parts_list.xlsx]
2018-07-12 enclosure rev0.1
    - updated z-axis_parts_plate.STL
    - added new blocker_cover.STL part
    - added new blocker_cover_endstop_v2.STL part
    - added corner covers
    - updated render
    [2020_corner_cover_mount.STL, 2020_corner_cover_mount_top.STL, 2020_corner_cover_mount_top_spool_holder.STL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]
2018-07-24 enclosure update
    [2020_bottom_corner_cover.STL, 2020_bottom_cover_glides_mount.STL, 2020_corner_cover_mount_top_screw_hole.STL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]
2018-08-08 enclosure update
    Enclosure printed parts ready for assembly.
    [door_hinge_1a.STL, door_hinge_1b.STL, fan_mount_v12.STL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]
2018-08-09 update
    part_list.xls cleanup and added latest renders
    [parts_list.xlsx]
2018-09-12 bondtech gears
    new extruder design withe bondtech gears and 3:1 ratio
    [bondtech_gear.STL, bondtech_gears_block_bottom.STL, bondtech_gears_block_top.STL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]
2018-09-13 update
    -updated all files with latest enclosure design.
    -added printed parts for bondtech extruder design
    [fan_mount_v11.STL, fan_mount_v12.STL, parts_list.xlsx]
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2018-09-14 bondtech update
    [5to3mm_bore.STL, 7to5mm_bore.STL, bondtech_gear.STL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]
2018-09-15 nozzle cleaner
    [2020_servo_holder.STL, wiper.STL]
2018-09-16 config update
    At winter couldn't test the max motor current in pursuit of safe temperatures. When summer has arrived i have lowered motor amps and forgot to change max speeds.
    [stepper_motor_speed.xlsx]
2018-09-16 nozzle wiper
    [2020_servo_holder.STL, wiper_v2.STL]
2018-09-17 part list update
    [parts_list.xlsx]
2018-09-25 config and software update
    added config changes needed for overkill serial filament menager (detector)
2018-09-25 filament detector code
    simple arduino code for nodeM esp8266 smoothieware filament detector with serial comunication
2018-10-02 major design update
    -bondtech extruder re-design (now it works perfect)
    -added nodeM esp8266 holder
    -added hall sensor filament detector
    [5to3mm_bore.STL, 5to3mm_bore_Long_v2.STL, 7to5mm_bore.STL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]
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2018-10-02 update
    filament_detector.ino major update:
    - use 2 inputs (microswitch, opto, hall-e etc.) to detect filament absence and control the 3dprinter suspend state by serial comand
    - semi-automatic filament changing
    *slide filament into spool sensor for automatic nozzle heatup (slide out to cooldown)
    *when heated up slide the filament into extruder sensor so it can be auto-loaded
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2018-12-14 bondtech update
    after some time of testing adding latest update.
    partlist:
    - 1x DIN 931 m5x40 (cutted to 24mm)
    - 1x MR 105 ZZ
    - 1x MF 105 ZZ
    - bontech gears 5mm bore version
    [1cm_test_cube.stl, 5to3mm_bore_Long_v2.STL, acin_cover.STL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]
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
